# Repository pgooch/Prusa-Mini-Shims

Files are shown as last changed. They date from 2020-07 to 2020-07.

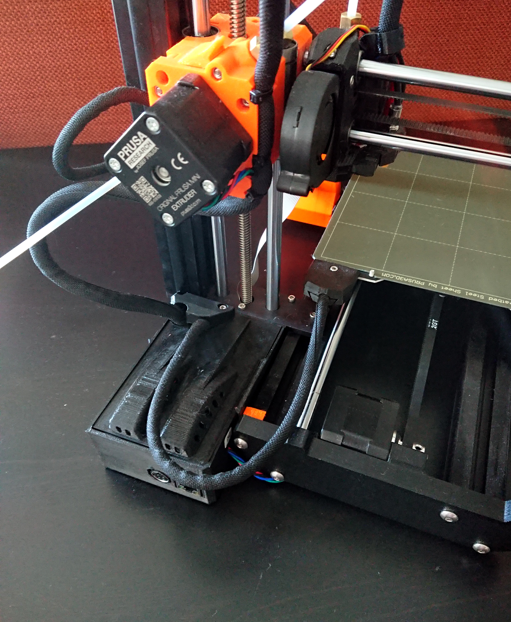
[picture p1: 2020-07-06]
Shim Installation Location.jpg

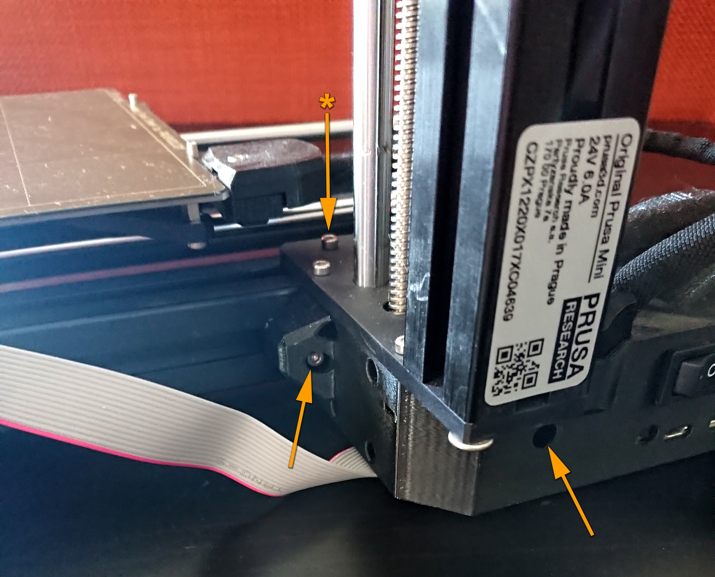
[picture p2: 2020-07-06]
Oh the Screws You'll Remove.jpg

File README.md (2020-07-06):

# Prusa Mini Shims

This github repo can also be found at the following location:

* [Thingiverse](https://www.thingiverse.com/thing:4378040)

If you have ant tips or a better method of doing this in general feel free to let me know or to make a pull request with the changes and I'll see that it's integrated into the hosted versions as well.

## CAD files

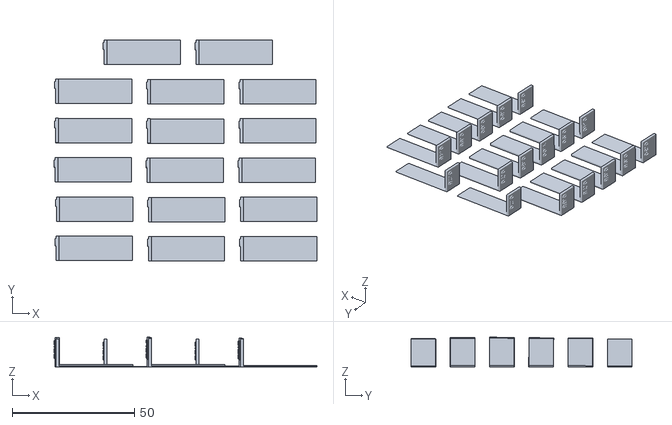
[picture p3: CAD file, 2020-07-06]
0.20mm to 1.00mm shims.stl
107.5 x 90.5 x 12.1

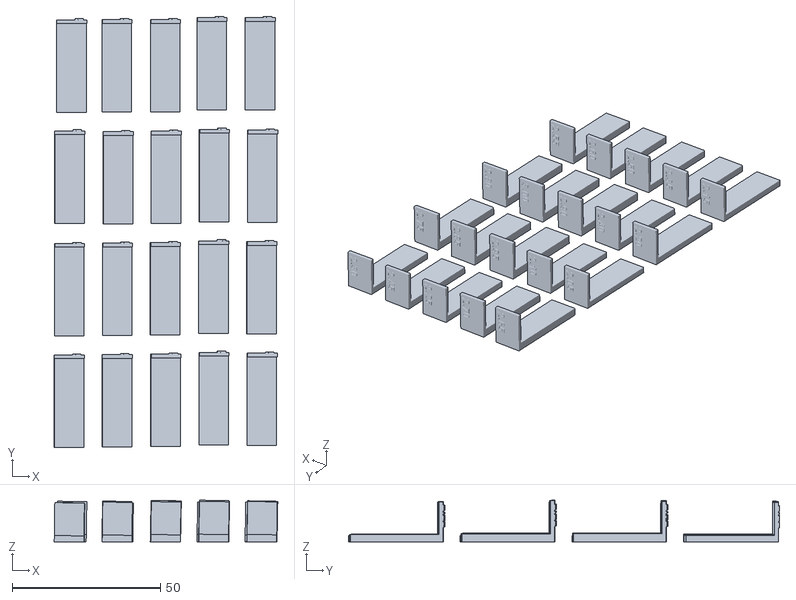
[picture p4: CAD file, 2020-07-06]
2.05mm to 3.00mm shims.stl
75.5 x 145.5 x 14.1

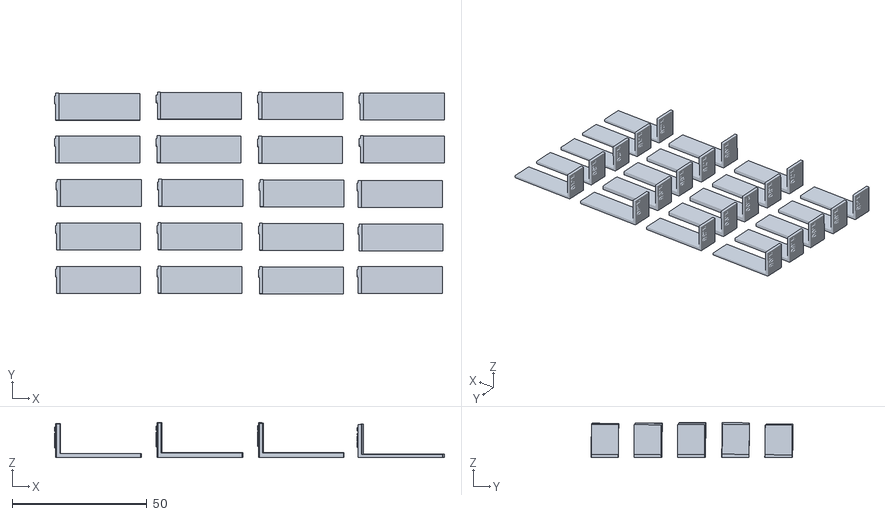
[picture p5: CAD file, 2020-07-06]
1.05mm to 2.00mm shims.stl
144.7 x 75.0 x 13.1

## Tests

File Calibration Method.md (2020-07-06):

# Prusa Mini X/Y Skew correction
This document will go through the process I used to calibrate my skewed Prusa Mini. As a foreword I'd like to make it clear that I am no a 3d printing expert, just a guy who was stupid enough to mess up my X/Y skew up and _just_ smart enough to fix it. Anything I state is this guide should not be taken as fact, I simply wrote this guide because there wasn't one on correcting this problem when it happened to me, but there are undoubtedly better ways to go about this. If you have any tips or a better solution leave it in the comments and they will be recompiled into this guide. I may also move this guide to GitHub if there is interest.

For all prints used when creating this guide I printed with Prusament PETG, previous to writing this I did the calibration with some cheap PLA I had on hand. Material seems to not matter much, and the only reason Prusament was used this time is so that the shim would match the rest of the printer. 

## The calibration print.
Before we start printing shims to fix the skew we should print a baseline. While you could use any pre-existing skew calibrator or create your own I suggest using [YACS (Yet Another Calibration Square) by Paciente8159](https://www.thingiverse.com/thing:2563185), it's the one I used and it prints quickly and seems to get the job done.

Calibration prints were sliced in PrusaSlicer at 0.2mm layer height with the default QUALITY setting. Prints should be made on a smooth surface as the texture could effect the layer height (and even small changes can cause inconsistency). You'll probably just want to keep the gCode on at hand so you don't have to re-slice between tests.

Also, __label your calibration prints__, or you will quickly forget which is which. Your gonna want to keep track of each print so you know if your skew is getting better or worse.

## The correction process.
First, print a calibration square. Then, measure the cross angles, A/C and B/D. In my case they were the following.

```
A/C = 141.6
B/D = 140.0
```
Now it's time to start placing shims and re-printing test calibration squares. From previous testing on this I found a good place to start is the difference of A/C and B/D, in my case that was 1.6mm, so that will be the fist shim I try. From there you can adjust the shim and print calibration squares until you are happy with the result. In general if A/C is longer than B/D you need a thicker shim, and the reverse is also true.

This time that was dead on and the 1.6mm shim corrected the skew. That was not the case the first time, and differences in prints and material may mean you making several attempts to get it dialed in. 

Just because I nailed it on the first attempt down't mean you will. I made countless shims and calibration prints the first time I was doing it in PLA, so don't fret if it doesn't work just swap out the shim and try again.

## Printing the shims
The shims were designed to be printed with the shimming side down to take advantage of the greater resolution when building layers. All prints were done with the 0.05MM ULTRADETAIL preset. It's a good idea to watch the first layer go down, as even minor problems with it can cause big problems down the line due to the tiny layer height.

When you slice you may notice this shimming surface has a slight taper to it. This was done in order to help the control box better sit against this shim and is intended.

Also note that printing at such high resolutions takes a long time. Printing 1 set took around 9 hours, so consider printing batches as needed so you can run multiple calibration squares between shim printing sessions. You could also use the adaptive layer heigh option, just make sure it's maxed out for the entire height of the shim. Even then there can be issues with the print, so the parts tend to need a bit of cleanup at the least. Just make sure to leave the shim surface alone or you'll make the process take longer by not knowing the _real_ thickness of the ones you've installed.

## Installing the shims
The shim goes on the back of the right Y axis bar, all the way up against the back lip that the control box uses for alignment. See "Shim Installation Location.jpg" (The first image on Thingiverse) for an image of the exact location, it's that odd orange bit between the axis rail and the control case.

To gain access to this location your going to need to remove a few screws. I have marked the locations on the "Oh the Screws You'll Remove.jpg" (The second image on Thingiverse) image. Technically I'm sure your _supposed_ to re-tighten them all when testing however I left the one marked with a * off, as well as the display (it was getting in the way) and it seems to have been OK.

If you shim is thick enough (around 1.5mm or greater) then the lip at the back of the printer will no longer hit the control box, in that case you just need to line it up as if it all fixed. You do have a little flexibility (maybe a millimeter or two) since the print bed is just a bit larger then the printers print area so exact positioning isn't important.

## How to know when your done
How fine you want to re-calibrate the printer is up to use. With a suitably fine measurement and enough time you could spend the rest of your life aiming for perfection. In reality however the 3D printing has tolerances (not just to to printer variation but also due to material properties). 

I found I had good results using the calipers as the gauge for my success. First I could measure A/C and use the locking screw on my calipers to hold the calibration square tight enough I could lift it off the table just by the calipers. Then, without touching the locking screw, I would slip the calibration square out of the calibers and kinda clip it on the other direction. Once it could pick up the square from all corners without touching the locking screw I considered it "good enough".

## What are all those STLs
The STLs can be broken into two categories. First is the master STL, this contains every shim on it's side (as thats how they were generated). If you want to print from this you'll need to break the STL apart and some them. There are more shims than will print on the Prusa mini at a single time, so after you have some idea how bad your skew is then you can print only a few around the target size.

The other STL files are shims grouped into roughly 1mm batches. These STL files are pre-faced and can be printed with minimal fuss, just remember to set it to the 0.05mm preset.
